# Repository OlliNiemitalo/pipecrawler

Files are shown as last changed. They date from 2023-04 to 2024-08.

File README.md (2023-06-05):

# Pipecrawler
Crawler for helical scanning of pipes. Work in progress.

The idea is to build a root imaging robot that travels and rotates inside a transparent pipe installed into the soil. The robot's camera will look at a helical track that overlaps itself by some amount on successive turns, so that the images or the video can be stitched together. Light sources can be attached to the robot. Attaching to the robot a phone with a camera may be the easiest option. A USB-C hub with external powering can be attached to the phone for charging and for peripherals such as a webcam for infrared imaging.

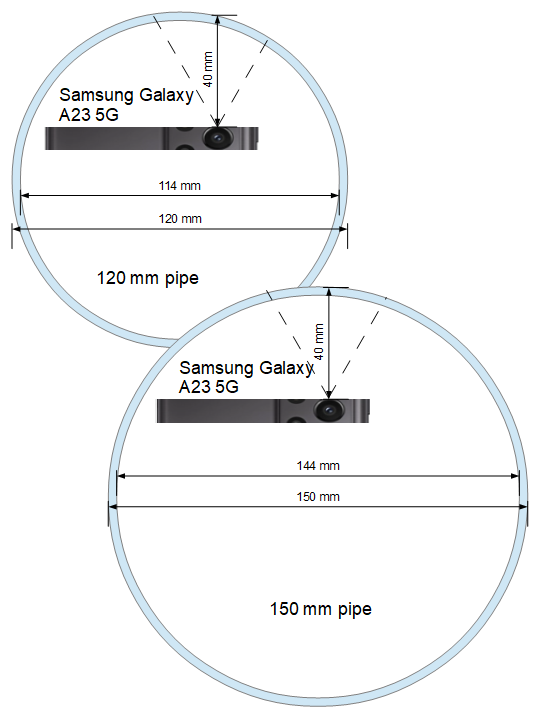
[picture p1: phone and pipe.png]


The initial design is for a pipe with an outer diameter of 120 mm and an inner diameter of 114 mm. PMMA is a good material for the pipe because it passes light wavelengths 400 nm to 1100 nm without significant attenuation. PMMA pipe with these dimensions is readily available at a cost around 50 €/m. A larger pipe with 150 mm outer diameter and a 144 mm inner diameter could alternatively be used, but it would be more expensive. Earth augers of both diameters are available for drilling the hole, with a cost around 250 € for the bit only.

A suitable budget phone costing around 200 € is [Samsung Galaxy A23 5G](https://www.gsmarena.com/samsung_galaxy_a23_5g-11736.php) with a 2 megapixel fixed-focus macro camera with a 30-50 mm (centered at 40 mm) focus distance and roughly a 60 degree horizontal field of view. If we would like to minimize motion blur in a 30 frames per second video, with a 180 degree shutter angle (meaning it uses only 1/60 s for exposure), to a width of 1 pixel in a 1600 horizontal pixels or 50 mm wide image, we'd need a horizontal scanning speed of at most 60 pixels per second, corresponding to 50 mm * (60 pixel / second) / (1500 pixel) = 2 mm / s. For a 120 mm pipe a single revolution is pi * 120mm = 377 mm / revolution. We'd thus want a scanning speed of 377 mm / revolution / (2 mm / s) = 189 s / revolution or 3 minutes / revolution or 1 / (3 minutes / revolution) = 0.33 RPM. Sparkfun has a [0.5 RPM DC gear motor](https://www.sparkfun.com/products/12348) which is about as slow as they get, so that would be our choice if choosing a DC motor. For a 1 m long pipe and an ascension of 2 cm / revolution, it would take 50 revolutions to travel the whole pipe. With that DC motor, that would take 50 revolutions / (0.5 RPM) = 1 hour and 40 minutes. If that is too long, then a faster motor and still photography is to be considered.

First we try to build the upper crawler unit that carries the camera. This should be rotated with respect to a lower crawler unit, by a slow motor.

## Prototype revision 1, 2023-04-21

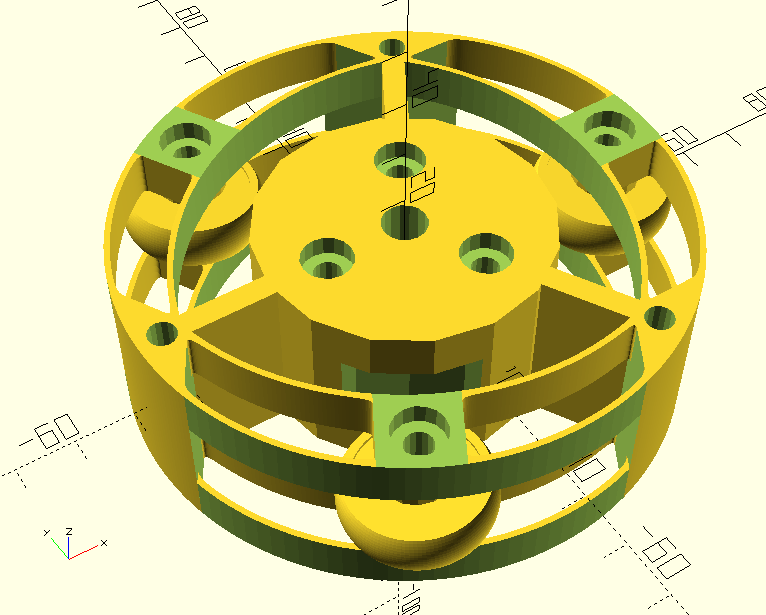
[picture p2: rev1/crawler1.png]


The upper unit was 3d-printed in PETG in two halves ("top" and "bottom"). The flexure springs felt too tight, likely demanding too much power from a motor due to too much resistance.

## Prototype revision 2, 2023-05-08

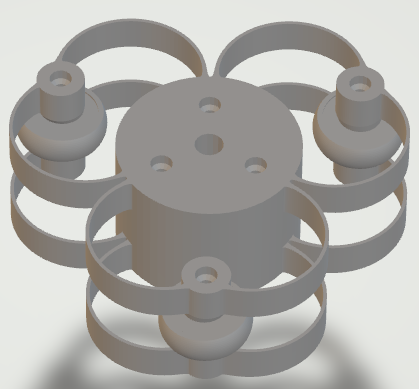
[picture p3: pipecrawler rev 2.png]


The second revision of the prototype has a simpler and a less stiff spring arrangement. The bolt size was reduced from M4 to M3 and overhangs in bolt head slots were reduced to 45 degs because there were print problems with those.

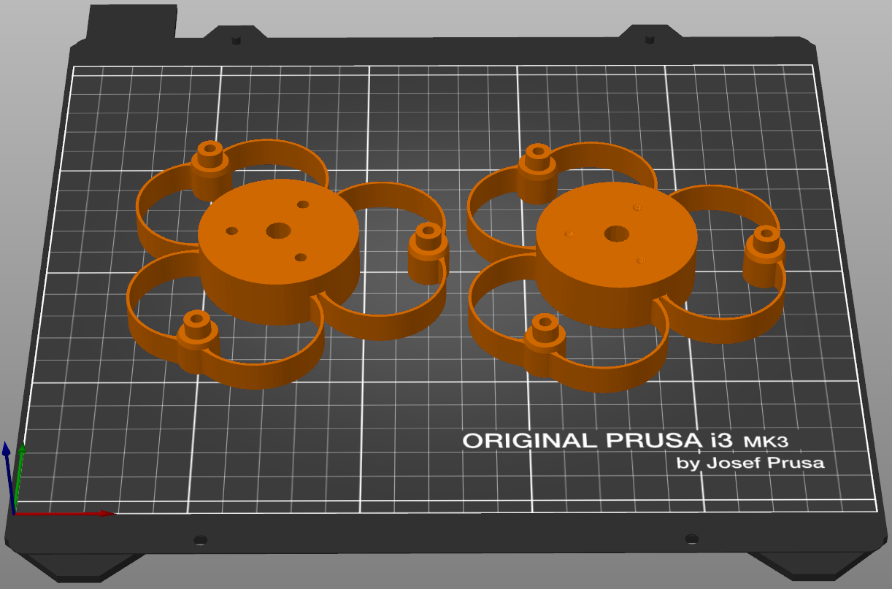
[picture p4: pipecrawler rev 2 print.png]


The wheels use "608" roller blade bearings with a 3d-printed tire made of Fiberlogy Fiberflex 40D, a thermoplastic polyester filament. Unfortunately it is a bit slippery but perhaps not as slippery as thermoplastic polyurethane (TPU). Layer changes in printing give small bumps; vase mode printing could be investigated, but it would require g-code editing.



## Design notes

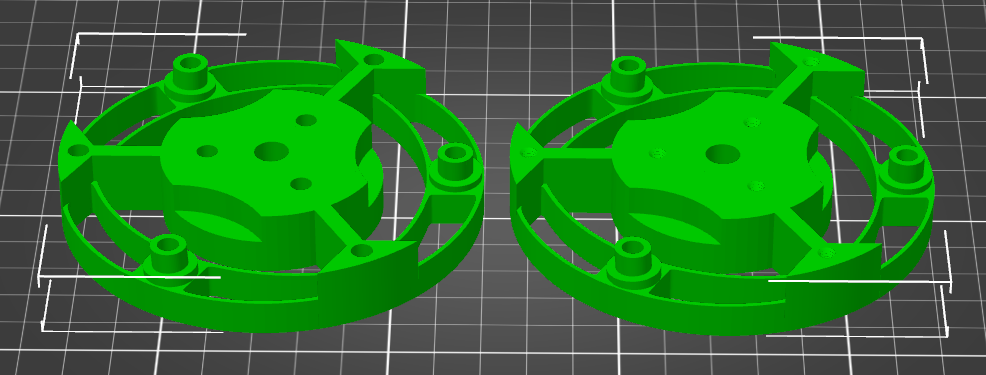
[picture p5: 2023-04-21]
rev1/pipecrawler.png

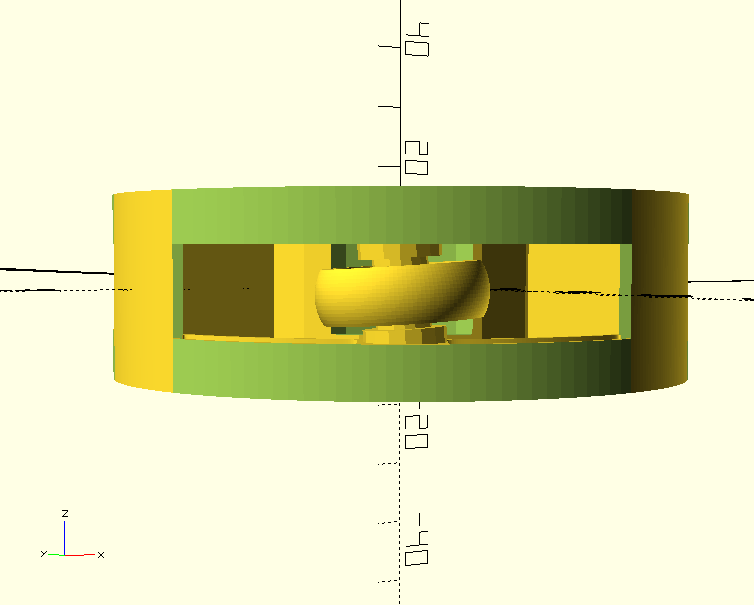
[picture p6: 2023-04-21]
rev1/crawler2.png

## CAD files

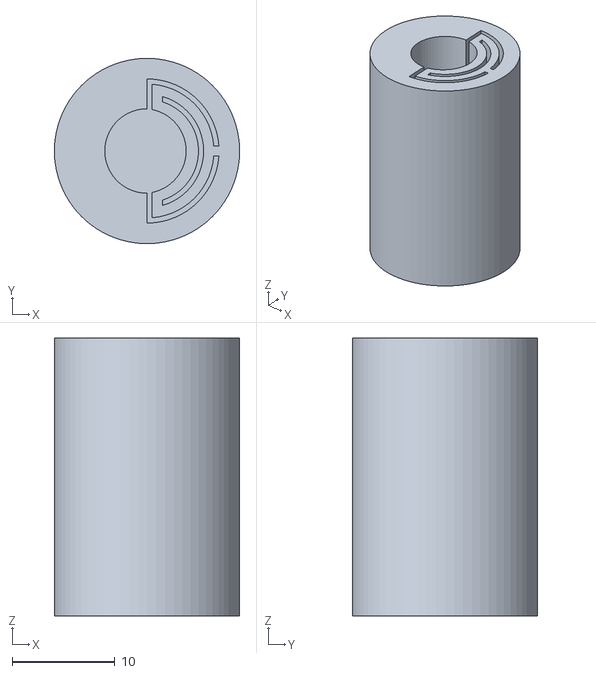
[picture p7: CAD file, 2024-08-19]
friction_clutch.stl
18.0 x 18.0 x 27.0

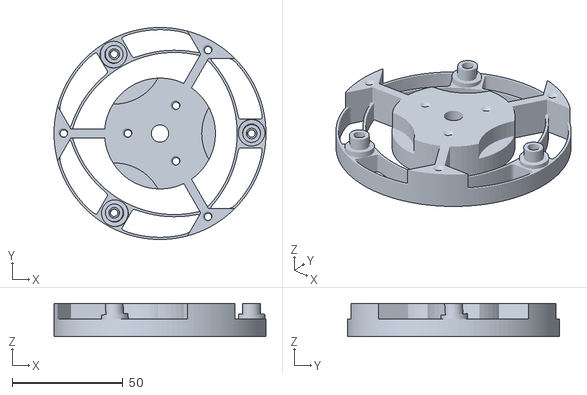
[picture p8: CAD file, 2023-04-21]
rev1/pipecrawler_upper_bottom.stl
95.6 x 95.6 x 15.0

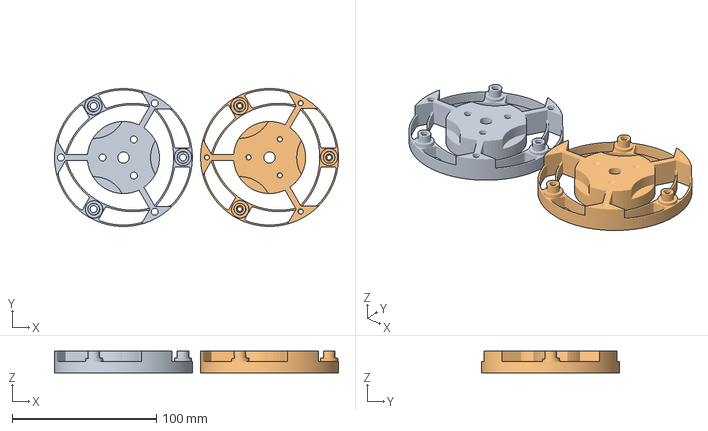
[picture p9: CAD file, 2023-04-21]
rev1/pipecrawler.3mf
196.9 x 95.6 x 15.0 mm
pipebot_upper_top.stl
pipescanner_upper_bottom.stl

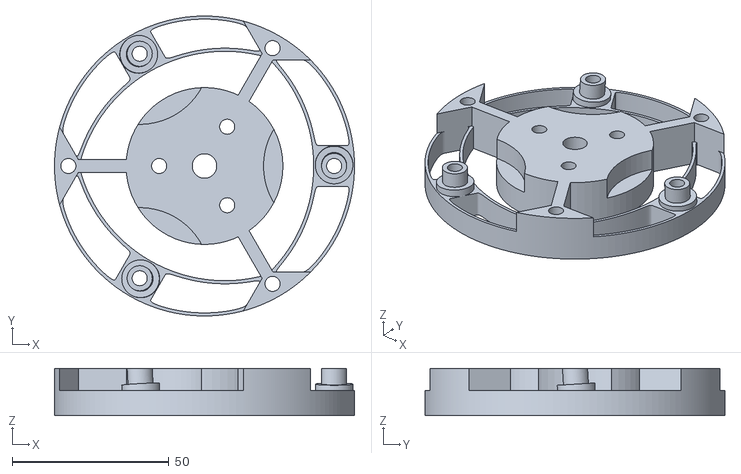
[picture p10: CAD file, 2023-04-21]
rev1/pipecrawler_upper_top.stl
95.6 x 95.6 x 15.0

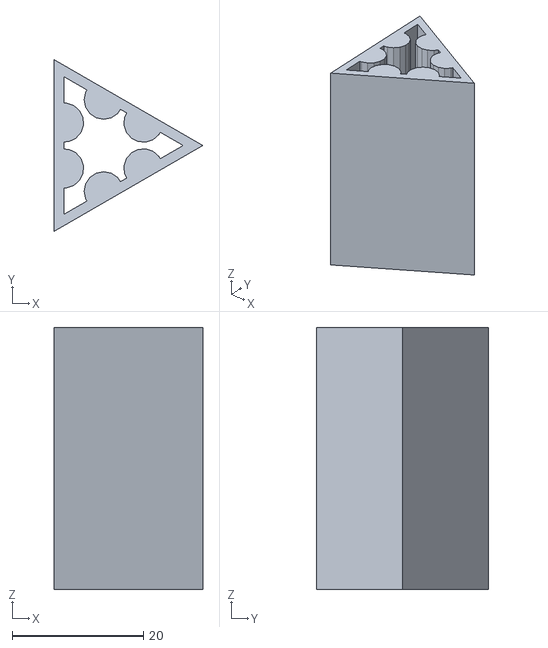
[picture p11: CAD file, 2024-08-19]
triangles.stl
22.7 x 26.2 x 40.0

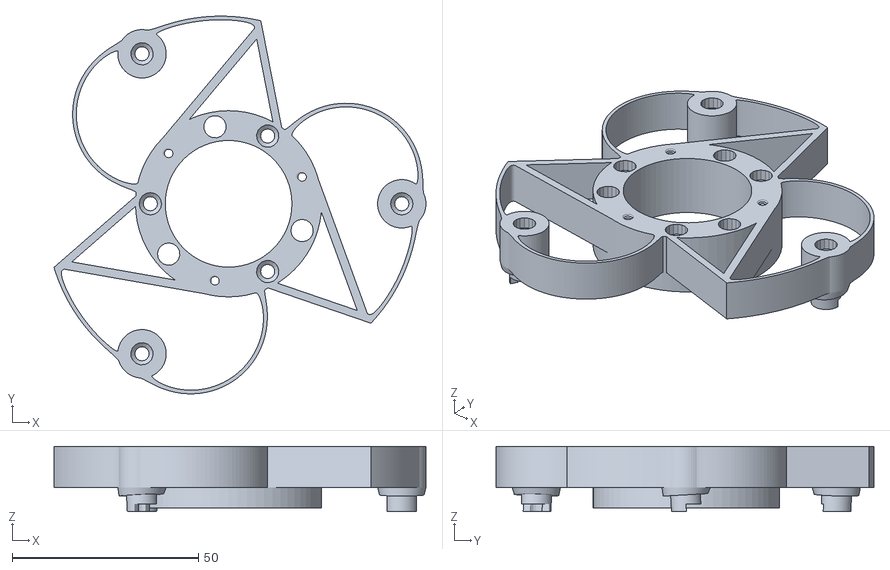
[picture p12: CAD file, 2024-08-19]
pipecrawler rev 3b top unit top part.stl
99.9 x 101.4 x 17.5

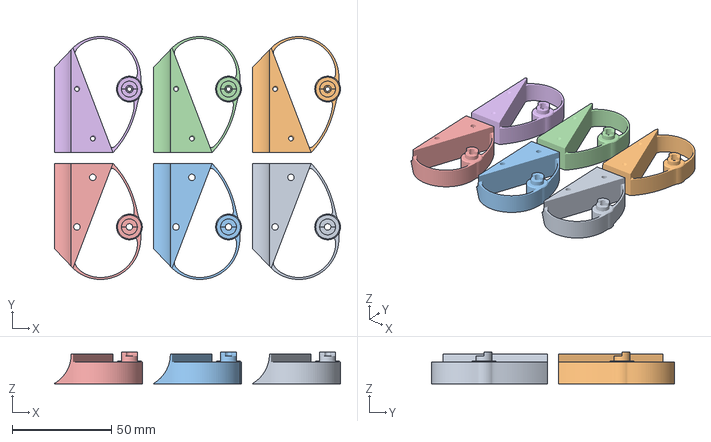
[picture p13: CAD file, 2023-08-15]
pipecrawler rev 3 lower unit.3mf
144.3 x 122.6 x 16.0 mm
pipecrawler rev 3 vertical wheel unit a.stl x 3
pipecrawler rev 3 vertical wheel unit b.stl x 3

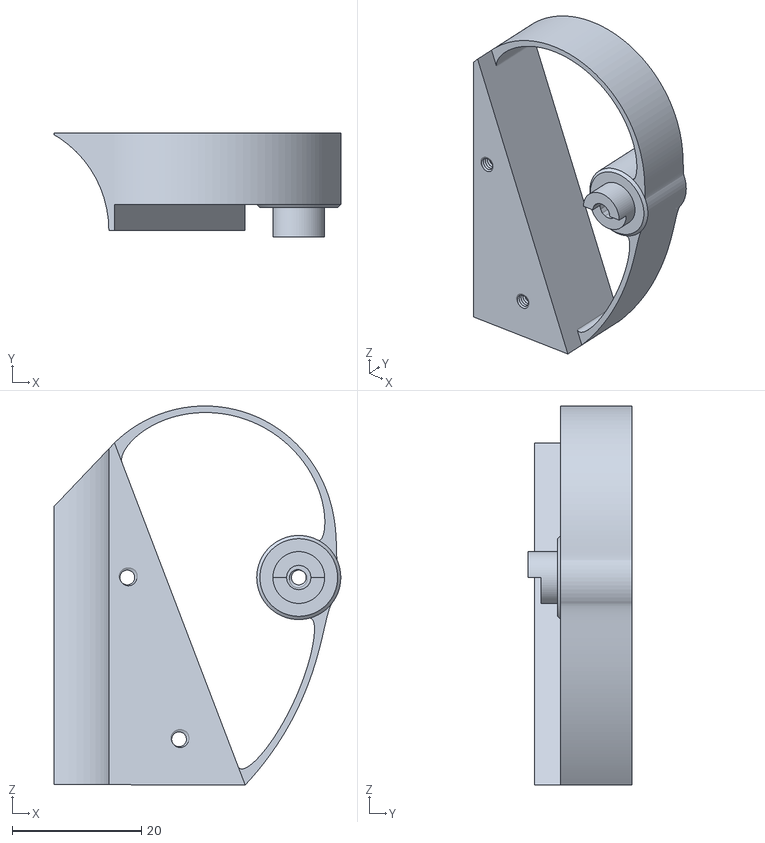
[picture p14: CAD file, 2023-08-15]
pipecrawler rev 3 vertical wheel unit b.stl
44.3 x 16.0 x 58.6

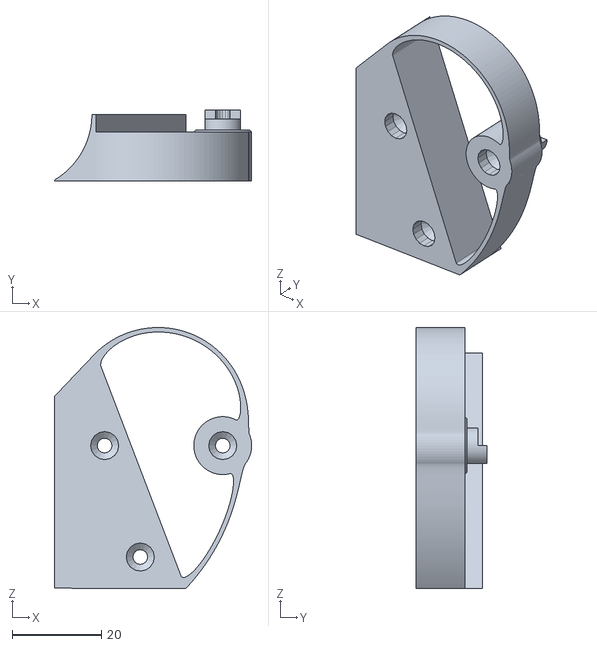
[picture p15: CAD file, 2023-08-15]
pipecrawler rev 3 vertical wheel unit a.stl
44.3 x 16.0 x 58.6

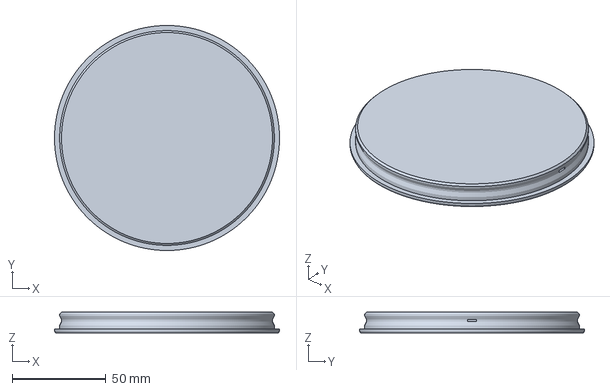
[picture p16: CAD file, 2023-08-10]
pipeplug.3mf
120.0 x 120.0 x 11.0 mm

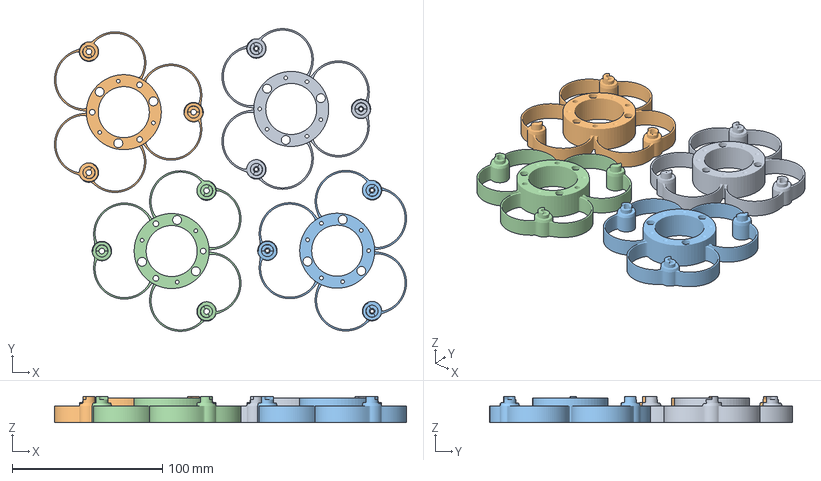
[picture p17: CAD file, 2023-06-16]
pipecrawler rev 3mf.3mf
234.6 x 201.7 x 17.5 mm
pipecrawler rev 2 top unit bottom part.stl
pipecrawler rev 2 top unit top part.stl
pipecrawler rev 2 bottom unit bottom part.stl
pipecrawler rev 2 bottom unit top part.stl

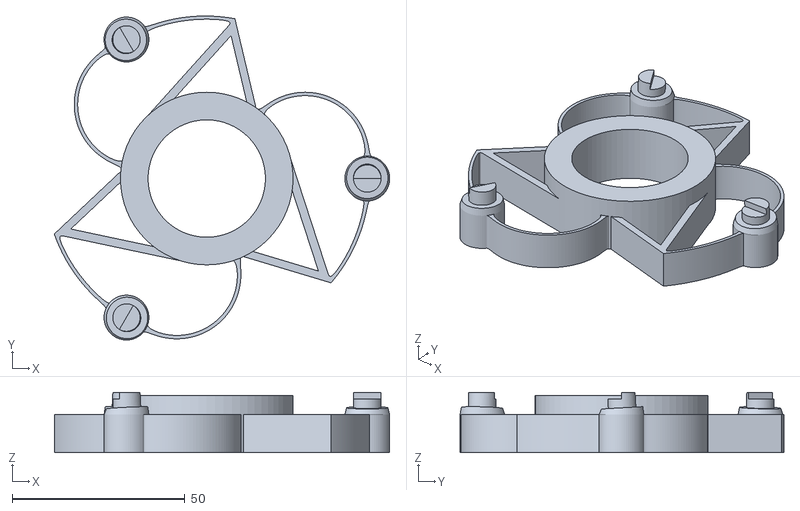
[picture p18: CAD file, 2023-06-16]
pipecrawler rev 3 test.stl
97.2 x 93.8 x 17.5

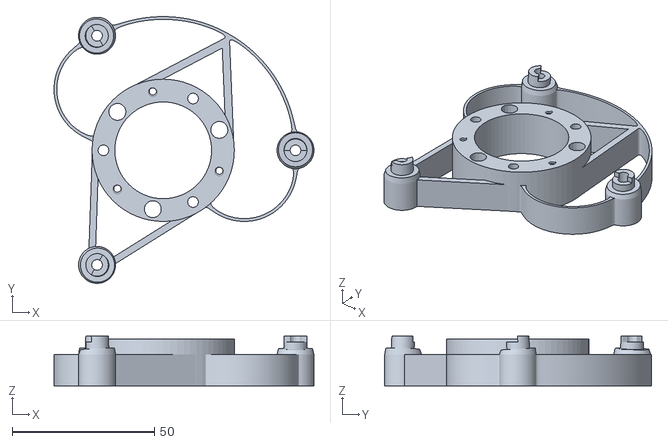
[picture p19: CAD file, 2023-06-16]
pipecrawler rev 3 bottom unit top part.stl
91.4 x 93.8 x 17.5

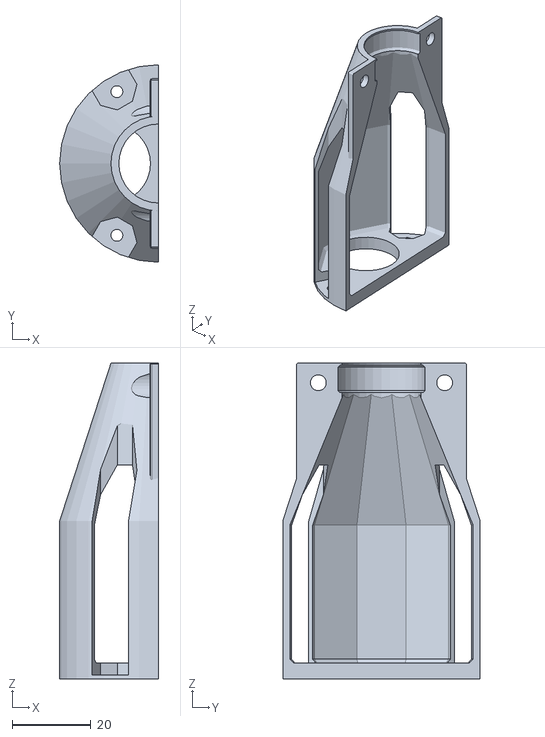
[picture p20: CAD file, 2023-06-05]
motor holder part 2.stl
25.0 x 50.0 x 80.0

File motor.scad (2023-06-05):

use <3rd-party/threads-scad/threads.scad>; // https://github.com/rcolyer/threads-scad

bearing_height = 7;
bearing_od = 22;
bearing_id = 8; // Not used
bearing_bevel = 0.5;

wheel_od = 26;
wheel_profile_r = 8;
wheel_lip_height = 0.5;
wheel_lip_width = 1; 

bolt_nominal_diameter = 3;
true_bolt_head_diameter = 6;
bolt_head_diameter = true_bolt_head_diameter + 4.5;
bolt_head_height = 3;

$fn=32;

body_id = 7.85;
body_od = 50;

shaft_support_h = 80;
shaft_support_t = 1;

conn_screw_r = 21;

motor_h = 25.5;
motor_d = 32.5;
motor_offset = (27.9 - 12.2) / 2;
motor_hole_d = (35.5 + 41.5) / 2;
motor_ear_w = 8.5;
motor_ear_t = 2;
motor_ear_d = 47 + 10;
motor_y = bolt_head_height + 1;

con_r = 15;

// Bearing
module bearing_cutout() {
    translate([0, 0, -wheel_lip_height - 10]) cylinder(wheel_lip_height + 10, bearing_od/2 - wheel_lip_width, bearing_od/2 - wheel_lip_width);
    cylinder(bearing_bevel, bearing_od/2 - bearing_bevel, bearing_od/2);
    translate([0, 0, bearing_bevel]) cylinder(bearing_height - 2*bearing_bevel, bearing_od/2, bearing_od/2);
    translate([0, 0, bearing_height - bearing_bevel]) cylinder(bearing_bevel, bearing_od/2, bearing_od/2 - bearing_bevel);
    translate([0, 0, bearing_height]) cylinder(wheel_lip_height, bearing_od/2 - wheel_lip_width, bearing_od/2 - wheel_lip_width);
}

if (false) ScrewHole( bolt_nominal_diameter, motor_y + motor_h, position=[motor_offset, motor_hole_d/2, 0]) ScrewHole( bolt_nominal_diameter, motor_y + motor_h, position=[motor_offset, -motor_hole_d/2, 0]) difference() {
    union() {
        minkowski() {
            translate([0, 0, shaft_support_h - 15 - 0.5]) cube([4-0.75, 42, 30], center=true);
            sphere(0.5, $fn=8);
        }
        cylinder(shaft_support_h/2, body_od/2, body_od/2);
        translate([0, 0, shaft_support_h/2]) cylinder(shaft_support_h/2, body_od/2, bearing_od/2 + shaft_support_t);
    }
    translate([0, 0, shaft_support_h/2 - 1]) rotate([0, 0, 360/24]) cylinder(shaft_support_h/2  - bearing_height, body_od/2 - shaft_support_t, bearing_od/2 - 1, $fn = 12);
    difference() {
        union() {
        translate([0, 0, 1 + bolt_head_height + 1]) rotate([0, 0, 360/24]) cylinder(shaft_support_h/2 - bolt_head_height - 2 - 1, body_od/2 - shaft_support_t, body_od/2 - shaft_support_t, $fn=12);
        translate([0, 0, 1 + bolt_head_height]) rotate([0, 0, 360/24]) cylinder(1, body_od/2 - shaft_support_t - 1, body_od/2 - shaft_support_t, $fn=12);
        }
        translate([motor_offset, 0, motor_y]) {
            difference() {
                translate([0, 0, (motor_h - motor_ear_t)/2]) cube([motor_ear_w, motor_ear_d, motor_h - motor_ear_t], center=true);
                cylinder(motor_h, motor_d/2, motor_d/2, $fn=64);
            }            
        }
    }
    translate([0, 0, shaft_support_h - bearing_height - 0.5]) bearing_cutout();
    translate([-50, 0, 50]) cube([100, 100, 120], center = true);
    for (i = [0: 3]) {
        rotate([0, 0, i*120]) {
            translate([conn_screw_r + (bolt_head_diameter - true_bolt_head_diameter)/2 - 1, 0, 1]) rotate([0, 0, 360/16]) cylinder(100, bolt_head_diameter/2 + 0.5, bolt_head_diameter/2 + 0.5, $fn=8);
            translate([conn_screw_r, 0, 0]) cylinder(1, bolt_nominal_diameter/2, bolt_nominal_diameter/2);
        }            
    }
    //translate([motor_offset, 0, motor_y]) motor();
    translate([motor_offset, motor_hole_d/2, motor_y + motor_h - motor_ear_t]) rotate([0, 0, 360/24 - 360/16]) cylinder(100, bolt_head_diameter/2 + 0.5, bolt_head_diameter/2 + 0.5, $fn=8);
    mirror([0, 1, 0]) translate([motor_offset, motor_hole_d/2, motor_y + motor_h - motor_ear_t]) rotate([0, 0, 360/24 - 360/16]) cylinder(100, bolt_head_diameter/2 + 0.5, bolt_head_diameter/2 + 0.5, $fn=8);
    {
    translate([-3, bearing_od/2 + 1 + 4, shaft_support_h - 5]) rotate([0, 90, 0]) cylinder(4, 2, 2);
    translate([2, bearing_od/2 + 1 + 4, shaft_support_h - 5]) rotate([0, 90, 0]) cylinder(10, 4, 4);
    translate([-2, bearing_od/2 + 1 + 4, shaft_support_h - 5]) rotate([0, -90, 0]) cylinder(10, 4, 4);
    }
    mirror([0, 1, 0]) {
    translate([-3, bearing_od/2 + 1 + 4, shaft_support_h - 5]) rotate([0, 90, 0]) cylinder(4, 2, 2);
    translate([2, bearing_od/2 + 1 + 4, shaft_support_h - 5]) rotate([0, 90, 0]) cylinder(10, 4, 4);
    translate([-2, bearing_od/2 + 1 + 4, shaft_support_h - 5]) rotate([0, -90, 0]) cylinder(10, 4, 4);
    }
    translate([10, 10, 0]) cylinder(5, 6, 6);
    translate([10, -10, 0]) cylinder(5, 6, 6);
    translate([-12, 0, 0]) cylinder(5, 10, 10);
}

module motor() {
    cylinder(motor_h, motor_d/2, motor_d/2);
    translate([0, 0, motor_h - motor_ear_t/2]) cube([motor_ear_w, motor_ear_d, motor_ear_t], center=true);
}

module con() ScrewHole(bolt_nominal_diameter, con_r - bolt_head_height, position=[0, -con_r + bolt_head_height, 2 + 5/2], rotation=[-90,0,0]) ScrewHole(bolt_nominal_diameter, con_r - bolt_head_height, position=[0, -(-con_r + bolt_head_height), 2 + 5/2], rotation=[90,0,0]) ScrewHole(bolt_nominal_diameter, con_r - bolt_head_height, position=[0, -con_r + bolt_head_height, 20 - (2 + 5/2)], rotation=[-90,0,0]) ScrewHole(bolt_nominal_diameter, con_r - bolt_head_height, position=[0, -(-con_r + bolt_head_height), 20 - (2 + 5/2)], rotation=[90,0,0]){
    difference() {
        union() {
            cylinder(20, con_r, con_r);
            translate([0, 0, 20]) cylinder(21, con_r, 8/2 + 2);
        }
        difference() {
            cylinder(7, 5/2, 5/2);
            translate([0, 2.5+4/2, 2.5 + 2]) cube([5, 5, 5], center = true);
            translate([0, -2.5-4/2, 2.5 + 2]) cube([5, 5, 5], center = true);
        }
        translate([0, 0, 7]) cylinder(2, 5/2, 8/2);
        translate([0, 0, 7 + 2]) cylinder(40-7, 8/2, 8/2);
        //translate([-50, 0, 50]) cube([100, 100, 120], center = true);
        {
        translate([0, con_r, 2 + 5/2]) rotate([90, 360/16, 0]) cylinder(bolt_head_height, true_bolt_head_diameter/2 + 1, true_bolt_head_diameter/2 + 1, $fn=8);
        translate([0, con_r, 20 - (2 + 5/2)]) rotate([90, 360/16, 0]) cylinder(bolt_head_height, true_bolt_head_diameter/2 + 1, true_bolt_head_diameter/2 + 1, $fn=8);
        }
        mirror([0, 1, 0]) {
        translate([0, con_r, 2 + 5/2]) rotate([90, 360/16, 0]) cylinder(bolt_head_height, true_bolt_head_diameter/2 + 1, true_bolt_head_diameter/2 + 1, $fn=8);
        translate([0, con_r, 20 - (2 + 5/2)]) rotate([90, 360/16, 0]) cylinder(bolt_head_height, true_bolt_head_diameter/2 + 1, true_bolt_head_diameter/2 + 1, $fn=8);
        }
    }    
}

translate([0, 0, motor_y + motor_h + 2]) con();

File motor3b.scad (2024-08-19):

use <3rd-party/threads-scad/threads.scad>; // https://github.com/rcolyer/threads-scad

use <friction_clutch.scad>;

fc_body_base_h = 2;  // Friction clutch: body base height
fc_body_r = 9;  // Friction clutch: body radius
fc_height=25;  // Friction clutch: mechanism height
fc_shaft_diam=8;  // Friction clutch: shaft diameter
fc_tol=0.1;  // Friction clutch: tolerance by which to increase shaft radius in model
fc_tight=0.4;  // Friction clutch: spring preloading shift length
fc_t=1;  // Friction clutch: spring thickness
fc_gap=0.5;  // Friction clutch: gap between mechanism parts
fc_support_h=3;  // Friction clutch: height of the thin, printing support part of the mechanism
fc_support_t=0.4;  // Friction clutch: thickness of the of the thin, printing support part of the mechanism

motor_diam = 25;
motor_h = 60;
motor_shaft_support_h = 3.6;
motor_shaft_h = 12.1 - motor_shaft_support_h;
motor_shaft_cut_h = 8;
motor_shaft_diam = 3.9;
motor_z = 0;

coupler_z = motor_z + motor_h + motor_shaft_support_h;

body_id = 34;
body_od = 50;
body_screw_r = (body_id/2 + body_od/2)/2;

bearing_z = coupler_z + motor_shaft_h + fc_body_base_h + fc_height;

motor_support_h = bearing_z + 10;
motor_support_t = 2;
motor_support_base_h = 2;

bolt_nominal_diameter = 3;
bolt_head_diameter = 10;
bolt_head_height = 3;

motor_gummy_w = 10;

if (true) translate([0, 0, coupler_z]) {
    difference() {
        cylinder(motor_shaft_h + fc_body_base_h + fc_height, fc_body_r, fc_body_r, $fn=32);
        translate([0, 0, motor_shaft_h + fc_body_base_h]) friction_clutch(height=fc_height + 1/4096, shaft_diam=fc_shaft_diam, tol=fc_tol, tight=fc_tight, t=fc_t, gap=fc_gap, support_h=fc_support_h, support_t=fc_support_t);
    }
}

if (true) {
    shifted_arc(h=motor_support_base_h, orb=body_od/2, ort=body_od/2, irb=body_id/2, irt=body_id/2, sxb=0, sxt=0, syb=0, syt=0, angle0=0, angle1=360, $fn=36);
    difference() {
        union() {
            translate([0, 0, motor_support_base_h])shifted_arc(h=motor_support_base_h, orb=body_od/2, ort=body_od/2, irb=body_od/2-motor_support_t-motor_support_base_h, irt=body_od/2-motor_support_t, sxb=0, sxt=0, syb=0, syt=0, angle0=0, angle1=360, $fn=36);
            difference() {
                translate([0, 0, motor_support_base_h*2]) shifted_arc(h=motor_support_h - motor_support_base_h*2, orb=body_od/2, ort=bearing_od/2+motor_support_t, irb=body_od/2-motor_support_t, irt=bearing_od/2, sxb=0, sxt=0, syb=0, syt=0, angle0=0, angle1=360, $fn=36);
                //for (i = [0:2]) rotate([0, 0, 360/6+i*360/3 + 360/72]) translate([-20, 0, coupler_z - motor_shaft_support_h]) rotate([0, 0, 360/32]) cylinder(motor_support_h, bolt_head_diameter/2, bolt_head_diameter/2, $fn=16);
                for (i = [0:2]) rotate([0, 0, i*360/3 + 360/72]) translate([0, -motor_gummy_w/2, coupler_z - motor_shaft_support_h]) cube([body_od/2, motor_gummy_w, motor_shaft_support_h], center=false);
            }
        }
        for (i = [0:2]) rotate([0, 0, i*360/3 + 360/72]) translate([-(body_od/2 + body_id/2)/2, 0, 0]) rotate([0, 0, 360/32]) cylinder(motor_support_h, bolt_head_diameter/2, bolt_head_diameter/2, $fn=16);
    }
}

bat_l = 70.5;

bearing_height = 7;
bearing_od = 22;
bearing_id = 8; // Not used
bearing_bevel = 0.5;

wheel_od = 26;
wheel_profile_r = 8;
wheel_lip_height = 0.5;
wheel_lip_width = 1; 

$fn=32;

shaft_support_h = 120;
shaft_support_t = 2;

conn_screw_r = 21;

con_r = 15;

// Bearing
module bearing_cutout() {
    translate([0, 0, -wheel_lip_height - 10]) cylinder(wheel_lip_height + 10, bearing_od/2 - wheel_lip_width, bearing_od/2 - wheel_lip_width);
    cylinder(bearing_bevel, bearing_od/2 - bearing_bevel, bearing_od/2);
    translate([0, 0, bearing_bevel]) cylinder(bearing_height - 2*bearing_bevel, bearing_od/2, bearing_od/2);
    translate([0, 0, bearing_height - bearing_bevel]) cylinder(bearing_bevel, bearing_od/2, bearing_od/2 - bearing_bevel);
    translate([0, 0, bearing_height]) cylinder(wheel_lip_height, bearing_od/2 - wheel_lip_width, bearing_od/2 - wheel_lip_width);
}

if (false) difference() {
    union() {
        minkowski() {
            translate([0, 0, shaft_support_h - 30 - 0.5]) cube([4-0.75, 42, 60], center=true);
            sphere(0.5, $fn=8);
        }
        cylinder(shaft_support_h/2, body_od/2, body_od/2);
        translate([0, 0, shaft_support_h/2]) cylinder(shaft_support_h/2, body_od/2, bearing_od/2 + shaft_support_t);
    }
    translate([0, 0, shaft_support_h/2 - 1]) rotate([0, 0, 360/24]) cylinder(shaft_support_h/2  - bearing_height, body_od/2 - shaft_support_t, bearing_od/2 - 1, $fn = 12);
    difference() {
        union() {
        translate([0, 0, 1 + bolt_head_height + 1]) rotate([0, 0, 360/24]) cylinder(shaft_support_h/2 - bolt_head_height - 2 - 1, body_od/2 - shaft_support_t, body_od/2 - shaft_support_t, $fn=12);
        translate([0, 0, 1 + bolt_head_height]) rotate([0, 0, 360/24]) cylinder(1, body_od/2 - shaft_support_t - 1, body_od/2 - shaft_support_t, $fn=12);
        }
        translate([motor_offset, 0, motor_y]) {
            difference() {
                translate([0, 0, (motor_h - motor_ear_t)/2]) cube([motor_ear_w, motor_ear_d, motor_h - motor_ear_t], center=true);
                cylinder(motor_h, motor_d/2, motor_d/2, $fn=64);
            }            
        }
    }
    translate([0, 0, shaft_support_h - bearing_height - 0.5]) bearing_cutout();
    // Half cut
    translate([-50, 0, shaft_support_h/2 - 5]) cube([100, 100, shaft_support_h + 20], center = true);
    // Main attachment screws
    for (i = [0: 3]) {
        rotate([0, 0, i*120]) {
            translate([conn_screw_r + (bolt_head_diameter - true_bolt_head_diameter)/2 - 1, 0, 1]) rotate([0, 0, 360/16]) cylinder(100, bolt_head_diameter/2 + 0.5, bolt_head_diameter/2 + 0.5, $fn=8);
            translate([conn_screw_r, 0, 0]) cylinder(1, bolt_nominal_diameter/2, bolt_nominal_diameter/2);
        }            
    }
    translate([motor_offset, motor_hole_d/2, motor_y + motor_h - motor_ear_t]) rotate([0, 0, 360/24 - 360/16]) cylinder(100, bolt_head_diameter/2 + 0.5, bolt_head_diameter/2 + 0.5, $fn=8);
    mirror([0, 1, 0]) translate([motor_offset, motor_hole_d/2, motor_y + motor_h - motor_ear_t]) rotate([0, 0, 360/24 - 360/16]) cylinder(100, bolt_head_diameter/2 + 0.5, bolt_head_diameter/2 + 0.5, $fn=8);
    {
    translate([-3, bearing_od/2 + 1 + 4, shaft_support_h - 5]) rotate([0, 90, 0]) cylinder(4, 2, 2);
    translate([2, bearing_od/2 + 1 + 4, shaft_support_h - 5]) rotate([0, 90, 0]) cylinder(10, 4, 4);
    translate([-2, bearing_od/2 + 1 + 4, shaft_support_h - 5]) rotate([0, -90, 0]) cylinder(10, 4, 4);
    }
    mirror([0, 1, 0]) {
    translate([-3, bearing_od/2 + 1 + 4, shaft_support_h - 5]) rotate([0, 90, 0]) cylinder(4, 2, 2);
    translate([2, bearing_od/2 + 1 + 4, shaft_support_h - 5]) rotate([0, 90, 0]) cylinder(10, 4, 4);
    translate([-2, bearing_od/2 + 1 + 4, shaft_support_h - 5]) rotate([0, -90, 0]) cylinder(10, 4, 4);
    }
    translate([10, 10, 0]) cylinder(5, 6, 6);
    translate([10, -10, 0]) cylinder(5, 6, 6);
    translate([-12, 0, 0]) cylinder(5, 10, 10);
}

module motor() {
    cylinder(motor_h, motor_d/2, motor_d/2);
    translate([0, 0, motor_h - motor_ear_t/2]) cube([motor_ear_w, motor_ear_d, motor_ear_t], center=true);
}
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

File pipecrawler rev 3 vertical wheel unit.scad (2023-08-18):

use <3rd-party/threads-scad/threads.scad>; // https://github.com/rcolyer/threads-scad

use <flexure.scad>;

pipe_id = 114;
pipe_od = 120;
pipe_height = 300;

wheel_bearing_with_washers_height = 7; // 10 if washers, 7 if without
wheel_bearing_height = 7;
wheel_bearing_od = 22;
wheel_bearing_id = 8;
wheel_bearing_bevel = 0.5;

wheel_od = 26;
wheel_height = 8;

wheel_tight = 2.5; // How much to increase the radius of the wheel location, in order to press the wheel against the pipe

bolt_nominal_diameter = 3;
bolt_head_diameter = 6;
bolt_head_height = 3;

wheel_support_height = 10.5;
wheel_vertical_clearance = 1;
wheel_horizontal_clearance = 10;
wheel_support_diam = 13;
wheel_shoulder_diameter = 12;

vertical_wheel_support_tiehole_x = 20;
vertical_wheel_support_tiehole_y = 0;
vertical_wheel_support_tieholeb_x = 28;
vertical_wheel_support_tieholeb_y = 25;

spring_radii = [19.5,19.5];
spring_shift_x = pipe_id/2 - wheel_od/2 + wheel_tight - spring_radii[0] + 5;
spring_shift_y = wheel_support_diam/2;
spring_angles = [135, 135, -8.27, -8.27];
spring_extra_t = [0.35, 0.35, 0.35, 0.35];
spring_extra_angles = [-38.65, -24.1];
spring_p = 2;
spring_t = 1;
spring_n = 64;

spring2_radii = [pipe_id/2 - wheel_od/2 + wheel_tight, pipe_id/2 - wheel_od/2 + wheel_tight];
spring2_shift_x = 4;
spring2_shift_y = 0.16;
spring2_angles = [6.1, 43];
spring2_extra_t = [0.35, 0.35, 0.35, 0.35];
spring2_extra_angles = [-39, 25];
spring2_p = 2;
spring2_t = 1;
spring2_n = 64;

spring2_support_extra = 2.885;

support_t = 5;

body_id = 34;
body_od = 50;

conn_screw_r = 21;

$fn = 16;

// Pipe
module pipe() {
    translate([0, 0, -wheel_bearing_with_washers_height/2 - wheel_vertical_clearance - wheel_support_height])
    difference() {
        cylinder(pipe_height, pipe_od/2, pipe_od/2, $fn = 32);
        cylinder(pipe_height, pipe_id/2, pipe_id/2, $fn = 32);
        // Cutout to show what's inside
        translate([0, -pipe_od/2, 0]) cube([pipe_od, pipe_od, pipe_height], center=false);
    }
}

// wheel_bearing
module wheel_bearing() {
    translate([0, 0, (wheel_bearing_with_washers_height - wheel_bearing_height)/2]) difference() {
        union() {
            cylinder(wheel_bearing_bevel, wheel_bearing_od/2 - wheel_bearing_bevel, wheel_bearing_od/2);
            translate([0, 0, wheel_bearing_bevel]) cylinder(wheel_bearing_height - 2*wheel_bearing_bevel, wheel_bearing_od/2, wheel_bearing_od/2);
            translate([0, 0, wheel_bearing_height - wheel_bearing_bevel]) cylinder(wheel_bearing_bevel, wheel_bearing_od/2, wheel_bearing_od/2 - wheel_bearing_bevel);    
        }
        cylinder(wheel_bearing_height, wheel_bearing_id/2, wheel_bearing_id/2);
    }
}

module wheel() {
    wheel_bearing();
    translate([0, 0, (wheel_bearing_with_washers_height - wheel_bearing_height)/2]) import("wheel.stl", convexity=3);
}

module sector(height, small_r, big_r, angles = [-60, 60], $fn = $fn) {    
    points = [
        for(step = [0:$fn]) [big_r * cos(angles[0] + (angles[1] - angles[0])*step/$fn), big_r * sin(angles[0] + (angles[1] - angles[0])*step/$fn)],
        for(step = [0:$fn]) [small_r * cos(angles[1] + (angles[0] - angles[1])*step/$fn), small_r * sin(angles[1] + (angles[0] - angles[1])*step/$fn)]
    ];
    linear_extrude(height) polygon(points);
}

module wheelsupport(top = false) {
// Wheels and springs
  {
    difference() {
        union() {
            mirror([0, top?1:0, 0]) {
            // Bent spring
            translate([spring_shift_x, spring_shift_y, -wheel_bearing_with_washers_height/2 - wheel_vertical_clearance - wheel_support_height]) color([1, 1, 0.5]) linear_extrude(wheel_support_height) spiral_flexure(spring_radii, spring_angles, spring_angles + spring_extra_angles, spring_t/2, spring_extra_t[0], spring_extra_t[2], spring_t/2, spring_extra_t[3], spring_extra_t[1], spring_p, spring_n);
            // Almost straight spring
            translate([spring2_shift_x, spring2_shift_y, -wheel_bearing_with_washers_height/2 - wheel_vertical_clearance - wheel_support_height]) mirror([0, 1, 0]) color([1, 1, 0.5]) linear_extrude(wheel_support_height) spiral_flexure(spring2_radii, spring2_angles, spring2_angles + spring2_extra_angles, spring2_t/2, spring2_extra_t[0], spring2_extra_t[2], spring2_t/2, spring2_extra_t[3], spring2_extra_t[1], spring2_p, spring2_n);
            // Spring supports
            translate([0, 0, -15]) linear_extrude(15) polygon([[38.22, -32.064], [8.7, -32], [8.7, 11], [18.02, 20.804]]);
    }

     translate([pipe_id/2 - wheel_od/2 + wheel_tight, 0, 0]) difference() {
        union() {
        // Wheel boltway
        translate([0, 0, -wheel_bearing_with_washers_height/2])    cylinder(wheel_bearing_with_washers_height / 2 + 5, wheel_bearing_id/2, wheel_bearing_id/2, $fn=64);
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

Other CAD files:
pipecrawler rev 3.3mf
pipecrawler rev 3 top unit top part.stl
rotor plug.stl
bat_holder.stl
motor2.scad
connector.stl
experimentplate.stl
flexure.scad
friction_clutch.scad
motor holder part 1.stl
pipe 120mm.3mf
pipe 120mm.scad
pipe 120mm.stl
pipecrawler rev 2 bottom unit top part.stl
pipecrawler rev 2 mockup.stl
pipecrawler rev 2 top unit top part.stl
pipecrawler rev 2.3mf
pipecrawler rev 2.scad
pipecrawler rev 3.scad
pipecrawler rev 3b.scad
pipeplug.scad
pipeplug.stl
proximity.scad
rev1/pipecrawler.scad
smooth wheel.3mf
smooth wheel.scad
smooth wheel.stl
wheel 26mm.stl
wheel.3mf
wheel.scad
wheel.stl

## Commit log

2023-05-08 print bed image, +3mf
    [pipecrawler rev 2.3mf]
2023-05-09 Add smooth wheel
    [pipecrawler rev 2.scad, smooth wheel.3mf, smooth wheel.scad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]
2023-08-15 stronger springs
    [flexure.scad, pipecrawler rev 3 lower unit.3mf, pipecrawler rev 3 vertical wheel unit a.stl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]
2023-08-18 flexure code rewrite
    [flexure.scad, pipecrawler rev 3 vertical wheel unit.scad]
2024-08-19 friction clutch
    [friction_clutch.scad, friction_clutch.stl, motor2.scad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]
